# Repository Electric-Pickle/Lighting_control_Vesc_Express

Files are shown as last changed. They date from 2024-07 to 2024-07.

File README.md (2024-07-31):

Lighting control Board For Vesc Based Pev's

THIS Branch in Being Developed (UNTESTED)

Features
* onboard 5v2a buck 160v in (turned on and off via CAN or SERIAL ports)
* 3 level shifted LED ws2812 or similar outputs, + 2 onboard 
* onboard USB-C (diode added for brains to be powered VIA usb)
* onboard CAN termination (solder jumper to activate)
* duck

Ordering,
* Gerbers are prepped for PCB fab and assembly service,
* board must be 0.6mm thick (has to be advanced anyways for the C3 mini) ¯\_(ツ)_/¯
* I've preordered the buck, but JLC doesnt stock it, easy enough to solder by hand(caution board is very dense)

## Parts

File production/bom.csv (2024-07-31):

Designator | Footprint | Quantity | Value | LCSC Part #
C1 | 0402 | 1 | 1uf | C52923
C10, C3 | 0402 | 2 | 10uF | C15525
C11, C4 | 0402 | 2 | 100n | C1525
C8, C9 | 0603 | 2 | 1uF | C15849
D1 | 0603 | 1 | D_Small | C143772
D2 | 0603 | 1 | red | C72044
D3, D4 | LED_WS2812B-2020_PLCC4_2.0x2.0mm | 2 | WS2812B-2020 | C965555
J1, J2, J9 | JST_GH_BM04B-GHS-TBT_1x04-1MP_P1.25mm_Vertical | 3 | Conn_01x04 | C161692
J10 | JST_GH_BM06B-GHS-TBT_1x06-1MP_P1.25mm_Vertical | 1 | Conn_01x06 | C189892
J5, J6 | JST_PH_B3B-PH-SM4-TB_1x03-1MP_P2.00mm_Vertical | 2 | Conn_01x03 | C160353
J7 | JST_PH_S3B-PH-SM4-TB_1x03-1MP_P2.00mm_Horizontal | 1 | Conn_01x03 | C265101
Q1, Q2, Q3 | SOT-523 | 3 | NMOS | C5224244
R1 | 0402 | 1 | 120r | C25079
R2, R3, R4 | 0402 | 3 | 3k3 | C25890
R5 | 0603 | 1 | 1k | C21190
R6, R7 | 0402 | 2 | 10k | C25744
SW1, SW2 | SW_Push_SPST_NO_Alps_SKRK | 2 | SW_Push | C720477
U1 | ESP32-C3-MINI-1-N4 | 1 | ESP32-C3-MINI-1-N4 | C2934569
U2 | ATA6561-GBQW-N | 1 | TCAN1042DRQ1 | C5308062
U3 | RSDW10-05H | 1 | DCDC | C5872541
U5 | SOT-223-3_TabPin2 | 1 | AMS1117-3.3 | C6186
U6 | SOT-666 | 1 | USBLC6-2P6 | C2827693

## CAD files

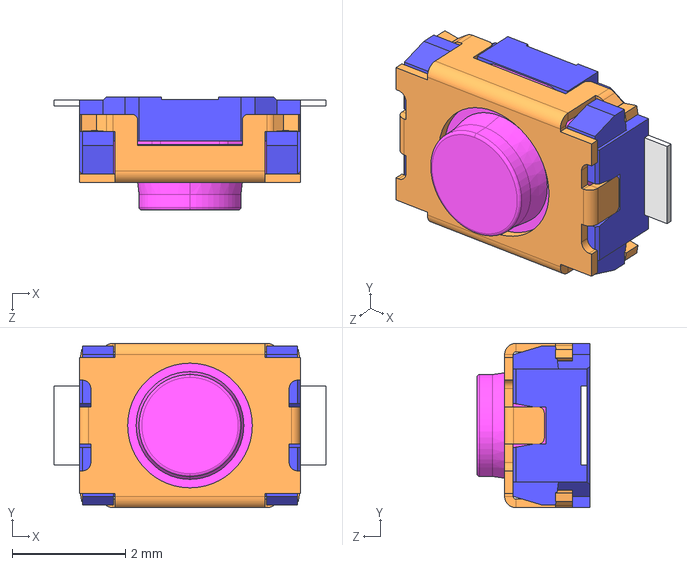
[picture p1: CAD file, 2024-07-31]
models/SKRKAH.STEP
4.80 x 2.90 x 2.00 mm

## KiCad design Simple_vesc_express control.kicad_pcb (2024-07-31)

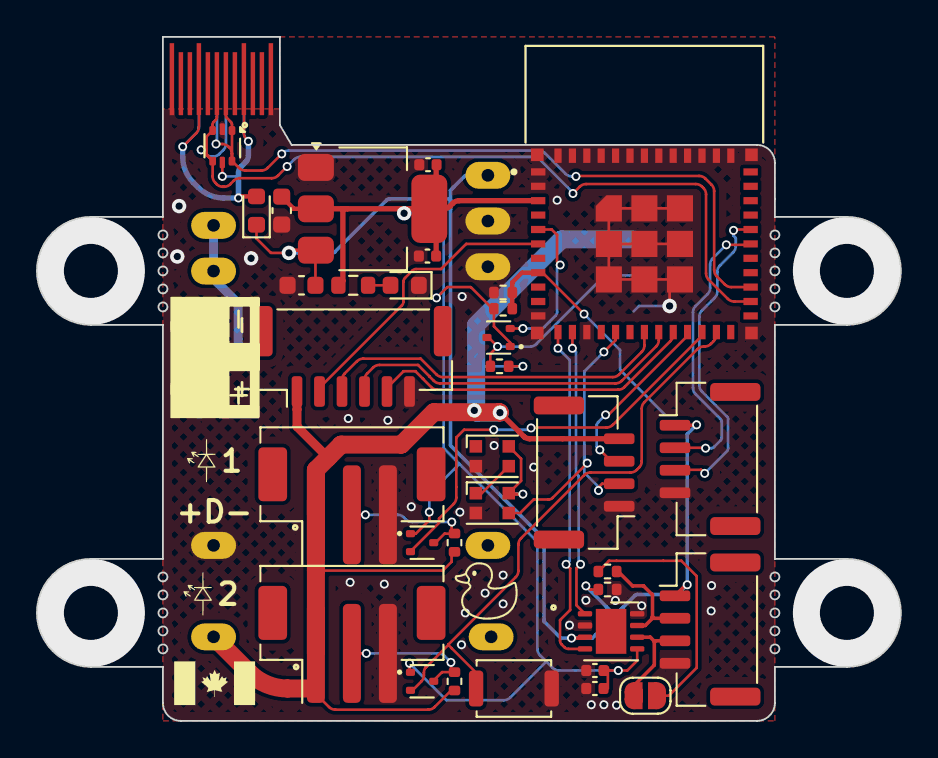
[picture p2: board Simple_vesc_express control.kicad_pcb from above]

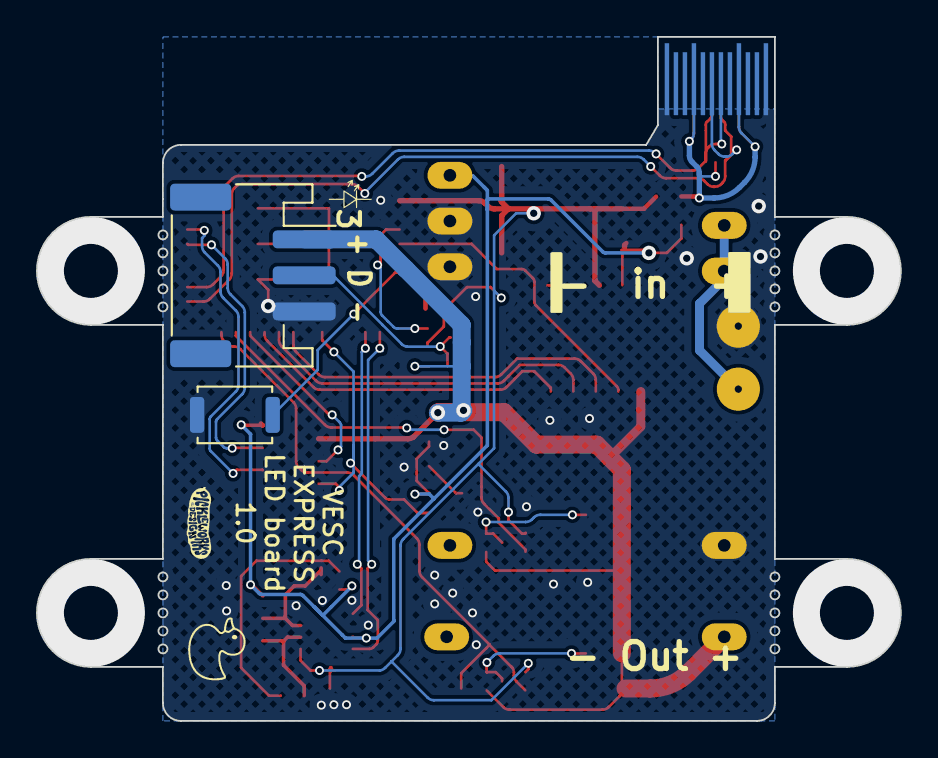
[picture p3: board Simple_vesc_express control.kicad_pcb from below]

Board: 2 copper layers, 48.0 x 38.0 mm, 38 parts (3 on the bottom side), 30 nets.

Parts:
C1: 1uf; R_0402_1005Metric
C3, C10: 10uF; C_0402_1005Metric
C4, C11: 100n; C_0402_1005Metric
C8, C9: 1uF; C_0603_1608Metric
D1: D_Small; D_0603_1608Metric
D2: red; LED_0603_1608Metric
D3, D4: WS2812B-2020; LED_WS2812B-2020_PLCC4_2.0x2.0mm
J1, J2, J9: Conn_01x04; JST_GH_BM04B-GHS-TBT_1x04-1MP_P1.25mm_Vertical
J4: USB_C_Receptacle_USB2.0; Cursed_usbc
J5, J6: Conn_01x03; JST_PH_B3B-PH-SM4-TB_1x03-1MP_P2.00mm_Vertical
J7: Conn_01x03; JST_PH_S3B-PH-SM4-TB_1x03-1MP_P2.00mm_Horizontal
J8: Conn_01x02; solder_power
J10: Conn_01x06; JST_GH_BM06B-GHS-TBT_1x06-1MP_P1.25mm_Vertical
JP1: Jumper_2_Open; SolderJumper-2_P1.3mm_Open_RoundedPad1.0x1.5mm
Q1, Q2, Q3: NMOS; SOT-523
R1: 120r; R_0402_1005Metric
R2, R3, R4: 3k3; R_0402_1005Metric
R5: 1k; R_0603_1608Metric
R6, R7: 10k; R_0402_1005Metric
SW1, SW2: SW_Push; SW_Push_SPST_NO_Alps_SKRK
U1: ESP32-C3-MINI-1-N4
U2: TCAN1042DRQ1; ATA6561-GBQW-N
U3: DCDC; RSDW10-05H
U5: AMS1117-3.3; SOT-223-3_TabPin2
U6: USBLC6-2P6; SOT-666

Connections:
!rst: C1.1, R6.1, SW2.1, U1.8 (EN)
+3V3: C3.1, C4.1, C9.1, C10.1, C11.1, Q1.1 (G), Q2.1 (G), Q3.1 (G), R5.1, R6.2, U1.3 (3V3), U2.5 (VIO), U5.2 (VO)
+5V: J5.1, J6.1, J7.1, J9.4, J10.1, R2.1, R3.1, R4.1, U3.14 (+VOUT)
+BATT: J8.1, U3.22 (+VIN), U3.23 (+VIN)
CAN+: J2.2, R1.1, U2.7 (CANH)
CAN-: J2.3, JP1.1 (A), U2.6 (CANL)
CAN_RX: U1.12 (IO0), U2.4 (RXD)
CAN_TX: U1.13 (IO1), U2.1 (TXD)
D+: J4.A6 (D+), J4.B6 (D+), U1.27 (IO19), U6.1 (I/O1), U6.6 (I/O1)
D-: J4.A7 (D-), J4.B7 (D-), U1.26 (IO18), U6.3 (I/O2), U6.4 (I/O2)
GND: C1.2, C3.2, C4.2, C8.2, C9.2, C10.2, C11.2, D2.1 (K), D3.2 (VSS), D4.2 (VSS), J1.4, J2.4, J4.A1 (GND), J4.A12 (GND), J4.B1 (GND), J4.B12 (GND), J5.3, J6.3, J7.3, J8.2, J9.1, J10.6, R7.2, SW1.2, SW2.2, U1.1 (GND), U1.2 (GND), U1.11 (GND), U1.14 (GND), U1.36 (GND), U1.37 (GND), U1.38 (GND), U1.39 (GND), U1.40 (GND), U1.41 (GND), U1.42 (GND), U1.43 (GND), U1.44 (GND), U1.45 (GND), U1.46 (GND), U1.47 (GND), U1.48 (GND), U1.49_1 (GND), U1.49_2 (GND), U1.49_3 (GND), U1.49_4 (GND), U1.49_5 (GND), U1.49_6 (GND), U1.49_7 (GND), U1.49_8 (GND), U1.49_9 (GND), U1.50 (GND), U1.51 (GND), U1.52 (GND), U1.53 (GND), U2.2 (GND), U2.8 (STB), U3.2 (-VIN), U3.3 (-VIN), U3.16 (-VOUT), U5.1 (GND), U6.2 (GND)
IO-3: J10.2, U1.6 (IO3)
IO-4: J10.3, U1.18 (IO4)
IO-5: J10.4, U1.19 (IO5)
IO-6: J10.5, U1.20 (IO6)
IO-7: J9.3, U1.21 (IO7)
IO-10: D4.3 (DIN), J9.2, U1.16 (IO10)
unnamed: D1.2 (A), J4.A4 (VBUS), J4.A9 (VBUS), J4.B4 (VBUS), J4.B9 (VBUS), U6.5 (VBUS)
unnamed: D2.2 (A), R5.2
unnamed: D3.3 (DIN), D4.1 (DOUT)
unnamed: JP1.2 (B), R1.2
RX: J1.2, U1.30 (RXD0)
TX: J1.3, U1.31 (TXD0)
en: C8.1, D1.1 (K), D3.4 (VDD), D4.4 (VDD), J1.1, J2.1, R7.1, U2.3 (VCC), U3.1 (ON/~OFF), U5.3 (VI)
led1 3v: Q1.2 (S), U1.22 (IO8)
led1 5v: J5.2, Q1.3 (D), R2.2
led2 3v: Q2.2 (S), SW1.1, U1.23 (IO9)
led2 5v: J6.2, Q2.3 (D), R3.2
led3 3v: Q3.2 (S), U1.5 (IO2)
led3 5v: J7.2, Q3.3 (D), R4.2

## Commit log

2024-07-31 first initial Commit
    [EV_battery_balance_board.kicad_pcb, EV_battery_balance_board.kicad_sch, SKRKAH.STEP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]
2024-07-31 changed usb powered parts
    [Simple_vesc_express control.kicad_pcb, Simple_vesc_express control.kicad_sch, bom.csv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]
2024-08-01 removed files, tracking
    [EV_battery_balance_board.kicad_pcb, EV_battery_balance_board.kicad_sch]
